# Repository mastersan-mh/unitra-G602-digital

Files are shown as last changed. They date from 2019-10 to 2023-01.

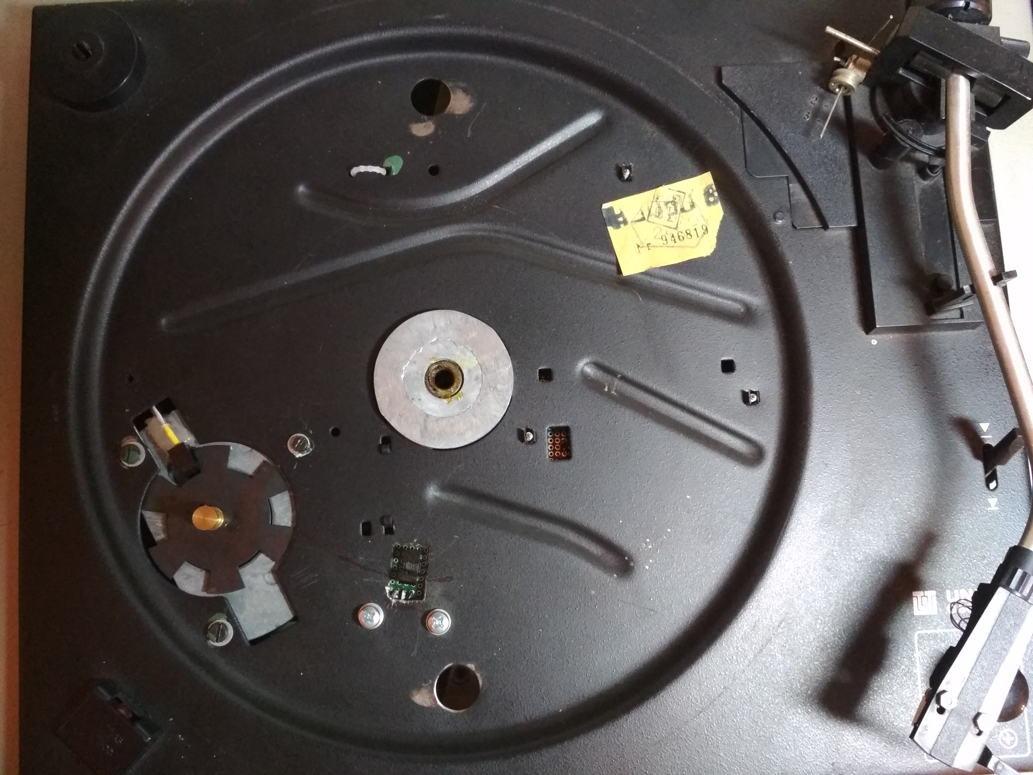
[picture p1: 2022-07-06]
rev1/pictures/IMG_20191018_183628.jpg

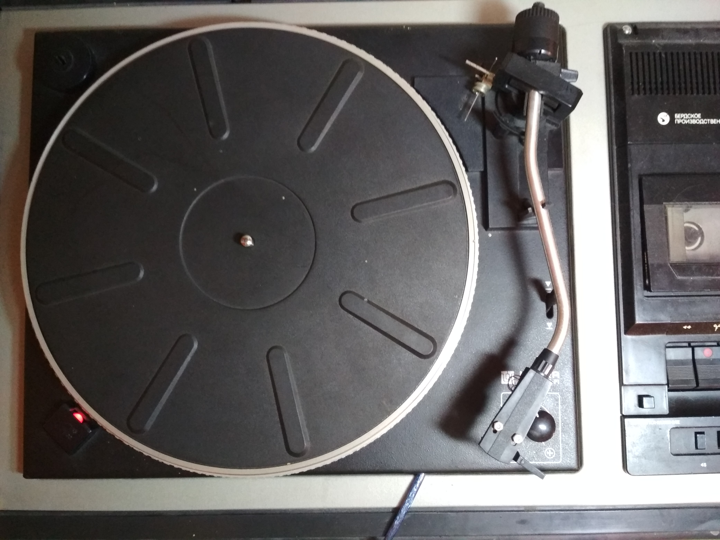
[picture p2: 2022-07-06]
rev1/pictures/IMG_20191018_184000.jpg

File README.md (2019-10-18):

I apologize to non-Russian-speaking users for the lack of information in English.

Данный проект был начат мной как попытка реанимировать старый электрофон Вега 119 с ЭПУ Unitra G602
(А ещё я люблю музыку и программирование).
Поскольку у оригинального устройства аналоговая плата управления пришла в полную негодность,
мной было принято решение о разработке цифрового управления.

В качестве платформы я выбрал Arduino Nano на микроконтроллере ATmega328p.
Это сильно упростило разработку платы и монтаж микросхем, особенно учитывая то, что это штучное устройство,
и весь монтаж я планировал провоизводить на макетную плату, используя только выводные компоненты.

Я процессе модернизации я старался как можно меньше модифицировать оригинальный компоненты,
однако, модификации подверглись:

1. Ведомый шкив. К нему снизу были приклеены 8 флажков.
Поскольку мне неизвестно передаточное число для шкива мотора и шкива диска,
я снимаю показания о скорости непосредственно со шкива диска.
Флажки изначально были подобраны такой высоты, чтобы шкив задевал ими за стол и не вращался.
Для того чтобы флажки стали нужной высоты, я покрыл наждачной бумагой стол ЭПУ, и несколько раз повернул шкив вокруг оси.
Как результат, флажки сточились до необходимой высоты.

2. В столе было прорезано одно отверстие, для того чтобы поместить туда оптический датчик для снятия показаний вращения диска,
и расширено одно из отверстий, чтобы в него вставить оптический датчик вращения двигателя.
Оригинальный датчик я не стал оставлять, поскольку его характеристики мне неизвестны,
а так же был сломан держатель лампы, которая освещала его.

3. Крепление двигателя было модифицировано, чтобы в него можно было вставить датчик вращения.

4. Оригиналная лампа стробоскопа была заменена на светодиод, который к тому же используется для индикации состояний.

5. Немного пришлось отрегулировать флажок автостопа, поскольку новый датчик немного не попал на то место, где находился старый датчик.

На самом деле, датчик вращения двигателя не нужен, я решил его установить в качестве эксперимена.

2019-09-29

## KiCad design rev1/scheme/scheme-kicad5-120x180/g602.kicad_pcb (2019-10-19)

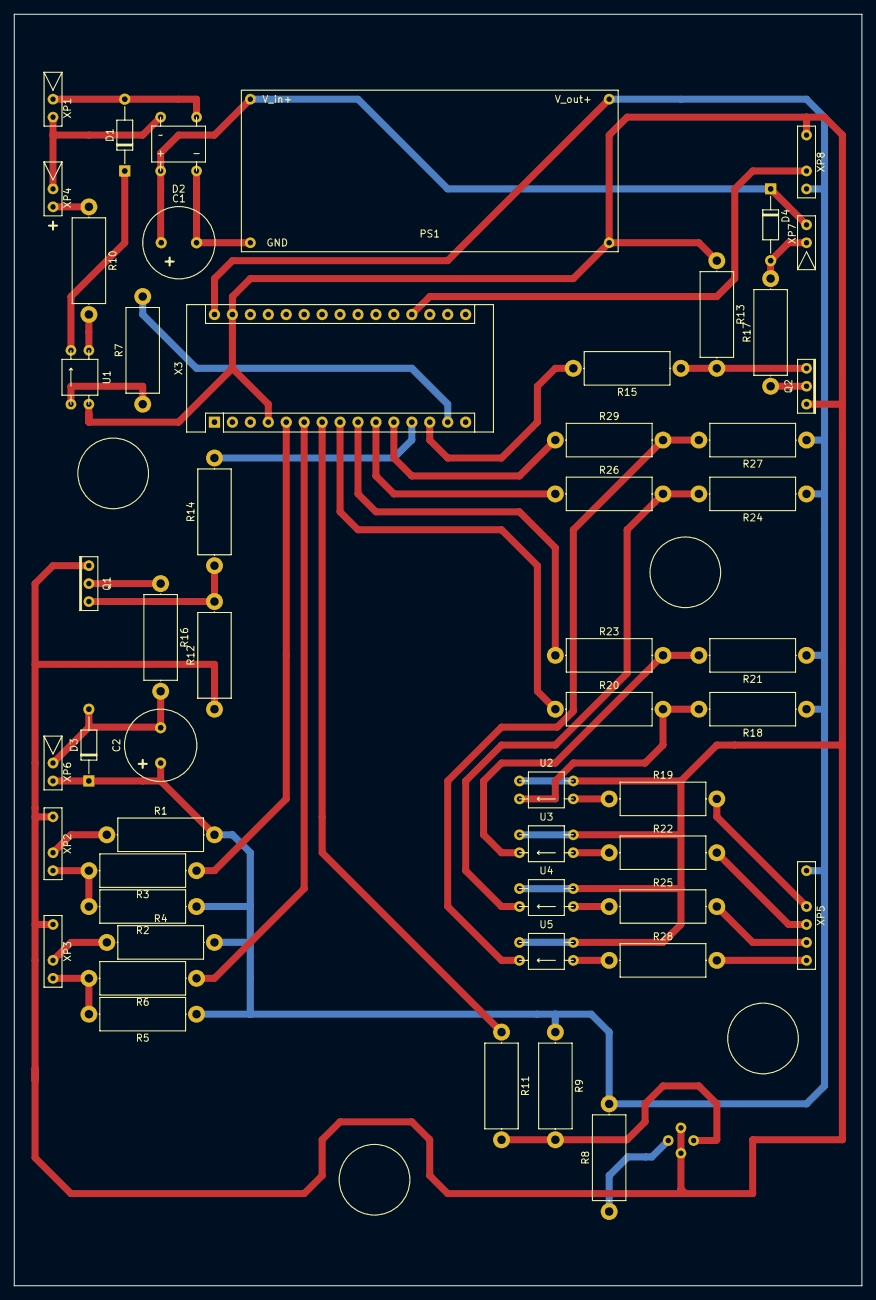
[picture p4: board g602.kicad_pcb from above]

Board: 2 copper layers, 120.0 x 180.0 mm, 53 parts (1 on the bottom side), 45 nets.

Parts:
C1: 2500uF; C_Radial_D10.0mm_H12.5mm_P5.00mm
C2: 2200uF; C_Radial_D10.0mm_H12.5mm_P5.00mm
D1, D3, D4: D; D_DO-35_SOD27_P10.16mm_Horizontal
D2: DF01M
PS1: DC-DC; DC-DC-converter
Q1, Q2: IRL2203NPBF
R1, R4, R7, R8, R19, R22, R25, R28: 510; R_Axial_DIN0414_L11.9mm_D4.5mm_P15.24mm_Horizontal
R2, R5, R9, R18, R21, R24, R27: 10k; R_Axial_DIN0414_L11.9mm_D4.5mm_P15.24mm_Horizontal
R3, R6, R11, R20, R23, R26, R29: 1k; R_Axial_DIN0414_L11.9mm_D4.5mm_P15.24mm_Horizontal
R10: 2k; R_Axial_DIN0414_L11.9mm_D4.5mm_P15.24mm_Horizontal
R12, R13: 50k; R_Axial_DIN0414_L11.9mm_D4.5mm_P15.24mm_Horizontal
R14, R15, R16: 10; R_Axial_DIN0414_L11.9mm_D4.5mm_P15.24mm_Horizontal
R17: 200; R_Axial_DIN0414_L11.9mm_D4.5mm_P15.24mm_Horizontal
U1, U2, U3, U4, U5: PC817
X3: arduino-nano; Arduino_Nano
X4: TCST1103; TCST1103-veritcal
XP1: ~~ 50Hz, 17V; Connector_01x02
XP2: Feedback_drive; Connector_01x03
XP3: Feedback_table; Connector_01x03
XP4: Strobe; Connector_01x02
XP5: Buttons; Connector_01x05
XP6: Motor; Connector_01x02
XP7: Microlift; Connector_01x02
XP8: Manual_speed_adjust; Connector_01x03

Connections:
GNDREF: PS1.3, Q1.3, Q2.3, R12.1, R13.1, U1.2, U2.2, U2.3, U3.2, U3.3, U4.2, U4.3, U5.2, U5.3, X3.4, X3.29, X4.2, X4.4, XP2.1, XP3.1, XP8.1
unnamed: C1.1, D2.1, D4.1, PS1.1, XP7.2
unnamed: C1.2, D2.2, PS1.2
unnamed: C2.1, D3.1, PS1.4, R1.2, R2.1, R4.2, R5.1, R8.2, R9.1, R18.1, R21.1, R24.1, R27.1, X3.30, XP5.1, XP6.2, XP8.3
unnamed: C2.2, D3.2, R16.2, XP6.1
unnamed: D1.1, U1.4
unnamed: D1.2, D2.3, XP1.1
unnamed: D2.4, XP1.2, XP4.1
unnamed: D4.2, R17.2, XP7.1
unnamed: Q1.1, R12.2, R14.1
unnamed: Q1.2, R16.1
unnamed: Q2.1, R13.2, R15.1
unnamed: Q2.2, R17.1
unnamed: R1.1, XP2.2
unnamed: R2.2, R3.2, XP2.3
unnamed: R3.1, X3.5
unnamed: R4.1, XP3.2
unnamed: R5.2, R6.2, XP3.3
unnamed: R6.1, X3.6
unnamed: R7.1, U1.1
unnamed: R7.2, X3.14
unnamed: R8.1, X4.1
unnamed: R10.1, XP4.2
unnamed: R10.2, U1.3
unnamed: R11.1, X3.7
unnamed: R9.2, R11.2, X4.3
unnamed: R14.2, X3.12
unnamed: R15.2, X3.13
unnamed: R18.2, R20.2, U2.4
unnamed: R19.1, U2.1
unnamed: R19.2, XP5.2
unnamed: R20.1, X3.8
unnamed: R21.2, R23.2, U3.4
unnamed: R22.1, U3.1
unnamed: R22.2, XP5.3
unnamed: R23.1, X3.9
unnamed: R24.2, R26.2, U4.4
unnamed: R25.1, U4.1
unnamed: R25.2, XP5.4
unnamed: R26.1, X3.10
unnamed: R27.2, R29.2, U5.4
unnamed: R28.1, U5.1
unnamed: R28.2, XP5.5
unnamed: R29.1, X3.11
unnamed: X3.19, XP8.2

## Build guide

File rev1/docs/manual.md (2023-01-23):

Руководство пользователя устройства электропроигрывающего Unitra-G602(digital)
========

** Содержание **

[TOCM]

[TOC]

# Описание режимов работы

## 1.1 Стоп

  + Описание

    Стол остановлен, лифт поднят.

  + Назначение органов управления

| Орган управления | Действие | Индикация |
| --- | --- | --- |
| `[45]` | Включение базовой скорости 45 об/мин | Нет |
| `[33]` | Включение базовой скорости 33 1/3 об/мин | Нет |
| `[АВТОСТОП]` | Нет | Нет |
| `[ПУСК]` | Переход в режим [1.2] | <1> |
| `[СТОП]` | Нет | Нет |
| `[СТОП]` в течении 5 секунд | Переход в режим [2.1] | <6> |
| `[РЕГУЛЯТОР]` | Нет | Нет |

## 1.2 Воспроизведение с фиксированной скоростью

  + Описание

    Воспроизведение с фиксированной скоростью, выбранной переключателями [45]/[33]. Стол вращается, лифт опущен.

  + Назначение органов управления

| Орган управления | Действие | Индикация |
| --- | --- | --- |
| `[45]` | Смотри режим [1.1] | Нет |
| `[33]` | Смотри режим [1.1] | Нет |
| `[АВТОСТОП]` | Включение режима автоматической остановки стола и поднятия лифта при достижении конца записи | Нет |
| `[ПУСК]` | Переход в режим [1.3] | <5> |
| `[СТОП]` | Переход в режим [1.1] | <2> |
| `[РЕГУЛЯТОР]` | Нет | Нет |

## 1.3 Воспроизведение с регулируемой скоростью

  + Описание

    Воспроизведение со скоростью, выбранной переключателями [45]/[33] с возможность ручной подстройки регулятором [РЕГУЛЯТОР]:
    для базовой скорости 45 - в диапазоне от 39 до 51, для базовой скорости 33 - в диапазоне от 27 до 39 об/мин.
    Стол вращается, лифт опущен.

  + Назначение органов управления

| Орган управления | Действие | Индикация |
| --- | --- | --- |
| `[45]` | Смотри режим [1.1] | Нет |
| `[33]` | Смотри режим [1.1] | Нет |
| `[АВТОСТОП]` | Смотри режим [1.2] | Нет |
| `[ПУСК]` | Переход в режим [1.2] | <5> |
| `[СТОП]` | Переход в режим [1.1] | <2> |
| `[РЕГУЛЯТОР]` | Ручная подстройка скорости воспроизведения | Нет |

## 2.1. Сервисный режим #1

  + Описание

    Режим настройки иглы: Стол остановлен, лифт опущен.

  + Назначение органов управления

| Орган управления | Действие | Индикация |
| --- | --- | --- |
| `[45]` | Смотри режим [1.1] | Нет |
| `[33]` | Смотри режим [1.1] | Нет |
| `[АВТОСТОП]` | Смотри режим [1.2] | Нет |
| `[ПУСК]` | Запуск режима | Нет |
| `[СТОП]` | Остановка режима / Переход в режим [2.2] | <2> / <4> |
| `[РЕГУЛЯТОР]` | Нет | Нет |

## 2.2. Сервисный режим #2

  + Описание

    Режим настройки скатывания иглы: Стол вращается, лифт опущен

  + Назначение органов управления

| Орган управления | Действие | Индикация |
| --- | --- | --- |
| `[45]` | Смотри режим [1.1] | Нет |
| `[33]` | Смотри режим [1.1] | Нет |
| `[АВТОСТОП]` | Смотри режим [1.2] | Нет |
| `[ПУСК]` | Запуск режима | Нет |
| `[СТОП]` | Остановка режима / Переход в режим [2.3] | <2> / <5> |
| `[РЕГУЛЯТОР]` | Нет | Нет |

## 3.3. Сервисный режим #3

  + Описание

    Настройки регулятора скорости внешними командами, принятыми из последовательного порта

  + Назначение органов управления

| Орган управления | Действие | Индикация |
| --- | --- | --- |
| `[45]` | Смотри режим [1.1] | Нет |
| `[33]` | Смотри режим [1.1] | Нет |
| `[АВТОСТОП]` | Смотри режим [1.2] | Нет |
| `[ПУСК]` | Запуск режима | Нет |
| `[СТОП]` | Остановка режима / Переход в режим [1.1] | <2> / <6> |
| `[РЕГУЛЯТОР]` | Нет | Нет |

# Индикация

| № | Тип мигания | Тип мигания | Значение |
| - | --- | --- | --- |
| 1 | `*-**--***---****----*****` | Ускоряющееся мигание | Запуск воспроизведения |
| 2 | `*****-----****----***---**--*` | Замедляющееся мигание | Остановка воспроизведения |
| 3 | `**` | 1 мигание | Включено автоматическое упавление скоростью / Переход в сервисный режим #1 |
| 4 | `**--**` | 2 мигание | Переход в сервисный режим #2 |
| 5 | `**--**--**` | 3 мигания | Включено ручное упавление скоростью / Переход в сервисный режим #3 |
| 6 | `*-*-*-*-*-*` | Частое мигание 6 раз | Переход в меню переключения сервисных режимов / Выход из меню сервисных режимов |
| 7 | `***---...` | медленное непрерывное мигание | Торможение стола выбегом |
| 8 | `*-...` | частое непрерывное мигание | Разгон стола |

# Протокол коммуникации посредством последовательного порта

## Назначение

Коммуникация посредством последовательного порта нужна для отладки изделия и для настройки коэффициентов регулятора скорости стола.

## Формат команды

Команды представляют собой набор ASCII-символов в 8-битной кодировке. Все числа представляются в 16-ричном формате,
цифры представлены множеством символов 0, 1, 2, 3, 4, 5, 6, 7, 8, 9, A, B, C, D, E, F.

* Формат кадра нижнего уровня:

`<start><frame><CRC><stop>`

`<start>`   - символ ':'.

`<stop>`    - Любой из символов LF (0x0A, '\n'), CR (0x0D, '\r') и их сочетания, 1-2 байта. В кадре ответа всегда LF.
              Любые внекадровые символы CR/LF игнорируются.

`<CRC>`     - Контрольная сумма <frame>, 16 бит, CRC-16-IBM, полином 0xA001.

* Кадр запроса:

`<frame> = <ruid><funcid><argc><argv>`

`<ruid>`     - [16 бит] Произвольное число, испрользуется для идентификации запроса и ответа. Ответ содержит то-же число, что и запрос.

`<funcid>`   - [8 бит] Код функции.

`<argc>`     - [8 бит] Количество аргументов [0; 8]

`<argv>`     - [16 * <argc> бит] Вектор аргументов.

* Кадр ответа:

`<frame> = <type>{ <ruid><error><resc><resv> | <eventid><resc><resv> }`

`<type>`     - [8 бит] тип ответа: 0x00 - ответ на вызов процедуры; 0x01 - событие

`<error>`    - [8 бит] Код ошибки.

`<eventid>`  - [8 бит] Код события.

`<resc>`     - [8 бит] Количество чисел в ответе.

`<resv>`     - [16 * <resc> бит] Вектор ответов.

Приечание: старший байт стоит первым (Network byte order)

## Функции

1. Прочитать значение количества имульсов на один оборот стола.

    * Запрос:

    `<funcid> = 0x00`

    `<argc> = 0`

    * Ответ:

    `<resc> = 1`

    `<argv[0]>` - Количество импульсов на один оборот стола.

    + Доступность: Все режимы

    + Пример:

      + Запрос: ":abcd0000ffb1\n"

      + Ответ: ":00abcd00010004087f\n"

2. Прочитать номер режима.

    * Запрос:

    `<funcid> = 0x01`

    `<argc> = 0`

    * Ответ:

    `<resc> = 1`

    `<resv[0]>` - номер режима (расшифровку смотри в ```Приложение:Коды значений```).

   * Доступность: Все режимы

   * Пример:

      + Запрос: ":abcd01006fb0\n"

      + Ответ: ":00abcd000110000b73\n"
             ":00abcd00011001cbb2\n"

3. Прочитать коэффициенты ПИД-регулятора: Kp, Ki, Kd

    * Запрос:

    `<funcid> = 0x02`

    `<argc> = 0`

    * Ответ:

    `<resc> = 6`

    `<resv[0]>`, `<resv[1]>` - `<Kp>`, пропорциональный коэффициент в формате signed-fixed-point-16.16.

    `<resv[2]>`, `<resv[3]>` - `<Ki>`, интегральный коэффициент в формате signed-fixed-point-16.16.

    `<resv[4]>`, `<resv[5]>` - `<Kd>`, дифференциальный коэффициент в формате signed-fixed-point-16.16

    * Доступность: Все режимы

4. Задать коэффициенты ПИД-регулятора: Kp, Ki, Kd

    * Запрос:

    `<funcid> = 0x03`

    `<argc> = 6`

    `<argv[0]>`, `<argv[1]>` - `<Kp>`, пропорциональный коэффициент в формате signed-fixed-point-16.16.

    `<argv[2]>`, `<argv[3]>` - `<Ki>`, интегральный коэффициент в формате signed-fixed-point-16.16.

    `<argv[4]>`, `<argv[5]>` - `<Kd>`, дифференциальный коэффициент в формате signed-fixed-point-16.16

    * Ответ:

    `<resc> = 0`

    + Доступность: Режим 2.3

5. Прочитать уставку скорости вращения стола

    * Запрос:

    `<funcid> = 0x04`

    `<argc> = 0`

    * Ответ:

    `<resc> = 2`

    `<resv[0]>`, `<resv[1]>` - Скорость вращения, число в диапазоне  `[0; 51 * <imp>]` импульсов/мин в формате signed-fixed-point-16.16.

    + Доступность: Все режимы

6. Задать уставку скорости вращения стола

    * Запрос:

    `<funcid> = 0x05`

    `<argc> = 2`

    `<argv[0]>`, `<argv[1]>` - Скорость вращения, число в диапазоне  `[ 0; 51 * <imp> ]` импульсов/мин в формате signed-fixed-point-16.16.

    * Ответ:

    `<resc> = 0`

    + Доступность: Режим 2.3

7. Прочитать действительную скорость вращения стола

    * Запрос:

    `<funcid> = 0x06`

    `<argc> = 0`

    * Ответ:

    `<resc> = 2`

    `<resv[0]>`, `<resv[1]>` - Скорость вращения, число в диапазоне  `[ 0; 51 * <imp> ]` импульсов/мин в формате signed-fixed-point-16.16.

    + Доступность: Все режимы

8. Запустить непрерывную передачу SP/PV

    * Запрос:

    `<funcid> = 0x07`

    `<argc> = 0`

    * Ответ:

    `<resc> = 0`

    + Доступность: Все режимы

9. Остановить непрерывную передачу SP/PV

    * Запрос:

    `<funcid> = 0x08`

    `<argc> = 0`

    * Ответ:

    `<resc> = 0`

    + Доступность: Все режимы

10. Сохранить конфигурацию

    * Запрос:

    `<funcid> = 0x09`

    `<argc> = 0`

    * Ответ:

    `<resc> = 0`

    + Доступность: Режим 2.3

## События

1. Событие переключения режима

     Событие инициируется при переключении режима работы.

    `<eventid>` = 0x00

    `<resc> = 1`

    `<resv[0]>` - Режим, смотри `<funcid> = 0x00`.

2. Событие SP/PV

     Событие всегда происходит через равные промежутки времени.

    `<eventid>` = 0x01

    `<resc> = 8`

    `<resv[0]>`, `<resv[1]>` - Время от запуска микроконтроллера, старшая и младшая часть, мс.

    `<resv[2]>`, `<resv[3]>` - Setpoint (Уставка), cкорость вращения, число в диапазоне  `[0; 51 * <imp>]` импульсов/мин в формате signed-fixed-point-16.16.

    `<resv[4]>`, `<resv[5]>` - Process Variable (Переменная процесса), cкорость вращения, число в диапазоне `[0; 51 * <imp>]` импульсов/мин в формате signed-fixed-point-16.16.

    `<resv[6]>`, `<resv[7]>` - Переменная управления в формате signed-fixed-point-16.16

    * Примечание:
        Переменная управления показывает значение, полученое с регулятора, однако, на привод отправляется только целая часть числа в диапазоне [0; 255]

# Приложение

## Коды ошибок

| Код(hex) | Описание |
| --- | --- |
| 0x00 | Нет ошибок |
| 0x01 | Команда недоступна в этом режиме |
| 0x02 | Неправильное количество аргументов |
| 0x03 | Значение агрумента вне диапазона |

## Коды значений

| Значение номера режима | Режим |
| --- | --- |
| 0x1000 | 1.1 |
| 0x1001 | 1.2 |
| 0x1002 | 1.3 |
| 0x2100 | 2.1: stopped |
| 0x2101 | 2.1: started |
| 0x2200 | 2.2: stopped |
| 0x2201 | 2.2: started |
| 0x2300 | 2.3: stopped |
| 0x2301 | 2.3: started |

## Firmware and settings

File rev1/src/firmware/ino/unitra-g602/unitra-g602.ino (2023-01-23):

#include "config.hpp"

#include "defs.hpp"

#include "AverageTinyMemory.hpp"

#include "G602.hpp"

#include "utils.hpp"

#include <nostd-main.h>
#include <nostd.h>

#include <util/atomic.h>
#include <EEPROM.h>

DEBUG_INIT_GLOBAL();

/*

/home/mastersan/progs/arduino-nightly/hardware/arduino/avr/cores/arduino
/home/mastersan/progs/arduino-nightly/hardware/arduino/avr/variants/standard
/home/mastersan/progs/arduino-nightly/hardware/tools/avr/avr/include




/home/mastersan/progs/arduino-nightly/hardware/tools/avr/bin/avr-g++
-c
-g
-Os
-w
-std=gnu++11
-fpermissive
-fno-exceptions
-ffunction-sections
-fdata-sections
-fno-threadsafe-statics
-Wno-error=narrowing
-flto
-w
-x c++
-E
-CC
-mmcu=atmega328p
-DF_CPU=16000000L
-DARDUINO=10807
-DARDUINO_AVR_NANO
-DARDUINO_ARCH_AVR
-I/home/mastersan/progs/arduino-nightly/hardware/arduino/avr/cores/arduino
-I/home/mastersan/progs/arduino-nightly/hardware/arduino/avr/variants/eightanaloginputs
/tmp/arduino_build_724020/sketch/unitra-g602.ino.cpp
-o /dev/null

*/

#define BOOL_TO_STR(xval) (xval ? "true" : "false")

//#define rotate_pulse_counter_t unsigned int
using rotate_pulse_counter_t = unsigned int;

static unsigned long g_time;
static unsigned long g_time_prev = 0;
static unsigned long c_cycletime = 0;

template<typename T>
T utils_map(T x, T in_min, T in_max, T out_min, T out_max)
{
    return (x - in_min) * (out_max - out_min) / (in_max - in_min) + out_min;
}

void dump_u8(
        const uint8_t * data ARG_UNUSED,
        unsigned size
)
{
    unsigned i;
    DEBUG_PRINT("  size8 = ");
    DEBUG_PRINTLN(size);
    for(i = 0; i < size; ++i)
    {
        DEBUG_PRINT("  data8[");
        DEBUG_PRINT(i);
        DEBUG_PRINT("]=");
        DEBUG_PRINTLN(data[i]);
    }
}

void dump_u16(
        const uint16_t * data ARG_UNUSED,
        unsigned size
)
{
    unsigned i;
    DEBUG_PRINT("  size16 = ");
    DEBUG_PRINTLN(size);
    for(i = 0; i < size; ++i)
    {
        DEBUG_PRINT("  data16[");
        DEBUG_PRINT(i);
        DEBUG_PRINT("]=");
        DEBUG_PRINTLN(data[i]);
    }
}

static void terminate_handler(const char * file, unsigned int line, int error)
{
#define BLINK_PERIOD_MS 250
    static long time_prev = 0;
    static long time;
    static bool on = true;

    unsigned long x = (unsigned long)file + line + error; /* to suppress warnings */

    while(1)
    {
        time = millis();
        if(time - time_prev >= BLINK_PERIOD_MS)
        {
            time_prev = time;
            if(x == 0)
            {
                digitalWrite(PIN_DO_STROBE_ERROR, on ? HIGH : LOW);
            }
            digitalWrite(PIN_DO_STROBE_ERROR, on ? HIGH : LOW);
            on = !on;
        }
    }
}

struct pulse
{
    unsigned long change_time; /**< Time of change */
    rotate_pulse_counter_t pulses; /**< Amount of clean pulses */
    rotate_pulse_counter_t bounces; /**< Amount of bounces (dirty pulses) */
};

static volatile struct pulse P_motor_rotate;
static volatile struct pulse P_table_rotate;

static void P_pulse_get(
        volatile struct pulse * pulse_in,
        bool reset,
        struct pulse * pulse_out
)
{
    pulse_out->change_time = pulse_in->change_time;
    pulse_out->pulses = pulse_in->pulses;
    pulse_out->bounces = pulse_in->bounces;
    if(reset)
    {
        pulse_in->pulses = 0;
        pulse_in->bounces = 0;
    }
}

void P_pulses_all_get(
        struct pulse * pulses_motor,
        struct pulse * pulses_table,
        bool reset
)
{
    ATOMIC_BLOCK(ATOMIC_FORCEON)
    {
        P_pulse_get(&P_motor_rotate, reset, pulses_motor);
        P_pulse_get(&P_table_rotate, reset, pulses_table);
    }
}

void P_config_store(const uint8_t * conf, size_t size)
{
    unsigned i;
    for(i = 0; i < size; ++i)
    {
        EEPROM.write(i, conf[i]);
    }
}

void P_config_load(uint8_t * conf, size_t size, bool * empty)
{
    bool tempty = true;
    unsigned i;
    for(i = 0; i < size; ++i)
    {
        for(i = 0; i < size; ++i)
        {
            conf[i] = EEPROM.read(i);
            if(conf[i] != 255)
            {
                tempty = false;
            }
        }
    }
    (*empty) = tempty;
}

static void P_event_strober(bool on)
{
    digitalWrite(PIN_DO_STROBE_ERROR, (on ? HIGH : LOW));
}

static void P_event_lift_up()
{
    digitalWrite(PIN_DO_LIFT, LOW);
    digitalWrite(PIN_DO_AUDIO_DENY, LOW);
}

static void P_event_lift_down()
{
    digitalWrite(PIN_DO_LIFT, HIGH);
    digitalWrite(PIN_DO_AUDIO_DENY, HIGH);
}

void P_motor_update(bool state, int output)
{
    if(state)
    {
        analogWrite(PIN_DO_ENGINE, output);
    }
    else
    {
        analogWrite(PIN_DO_ENGINE, 0);
    }
}

static void P_pulses_get(unsigned * motor_dpulses, unsigned * table_dpulses)
{
    struct pulse m_pulse;
    struct pulse t_pulse;
    P_pulses_all_get(&m_pulse, &t_pulse, true); /* reset */
    (*motor_dpulses) = m_pulse.pulses;
    (*table_dpulses) = t_pulse.pulses;

#if 0
    DEBUG_PRINT(g_time);

    DEBUG_PRINT("\tpulses ");
    DEBUG_PRINT(t_pulse.pulses);
    DEBUG_PRINT("\tbounces ");
    DEBUG_PRINT(t_pulse.bounces);

    DEBUG_PRINTLN();
#endif

}

static G602 g602(
    P_config_store,
    P_config_load,
    P_event_strober,
    P_event_lift_up,
    P_event_lift_down,
    P_motor_update,
    P_pulses_get
);

void P_pulses_init(volatile struct pulse * pulse)
{
    pulse->change_time = g_time;
    pulse->pulses = 0;
    pulse->bounces = 0;
}

static void P_pulse_update(volatile struct pulse * pulse, unsigned long bounce_time)
{
    if(g_time - pulse->change_time >= bounce_time)
    {
        ++(pulse->pulses);
    }
    else
    {
        ++(pulse->bounces);
    }
    pulse->change_time = g_time;
}

void drive_rotate_pulse_update(void)
{
    P_pulse_update(&P_motor_rotate, DI_MOTOR_DEBOUNCE_TIME);
}

void table_rotate_pulse_update(void)
{
    P_pulse_update(&P_table_rotate, DI_TABLE_DEBOUNCE_TIME);
}

static AverageTinyMemory potentiometer_avg(DI_POTENTIOMETER_FACTOR);

void setup()
{
    Serial.begin(9600);

    DEBUG_PRINT_INIT();

    g_time = millis();

    nostd::set_fatal(terminate_handler);
    /* INFO: разомкнуто = HIGH */

    /* gauges */
    pinMode(PIN_DI_GAUGE_DRIVE_ROTATEPULSE, INPUT_PULLUP);
    attachInterrupt(PIN_DI_2_INTERRUPT, drive_rotate_pulse_update, FALLING);
    pinMode(PIN_DI_GAUGE_TABLE_ROTATEPULSE, INPUT_PULLUP);
    attachInterrupt(PIN_DI_3_INTERRUPT, table_rotate_pulse_update, FALLING);

    pinMode(PIN_DI_GAUGE_STOP         , INPUT_PULLUP);
    /* buttons */
    pinMode(PIN_DI_BTN_45_33   , INPUT_PULLUP);
    pinMode(PIN_DI_BTN_AUTOSTOP, INPUT_PULLUP);
    pinMode(PIN_DI_BTN_START   , INPUT_PULLUP);
    pinMode(PIN_DI_BTN_STOP    , INPUT_PULLUP);

    pinMode(PIN_DO_ENGINE      , OUTPUT);
    pinMode(PIN_DO_LIFT        , OUTPUT);
    pinMode(PIN_DO_STROBE_ERROR, OUTPUT);
    pinMode(PIN_DO_AUDIO_DENY  , OUTPUT);

    analogWrite(PIN_DO_ENGINE, 0);
    digitalWrite(PIN_DO_STROBE_ERROR, HIGH);
    digitalWrite(PIN_DO_AUDIO_DENY  , LOW);

    analogReference(DEFAULT);

    P_pulses_init(&P_motor_rotate);
    P_pulses_init(&P_table_rotate);

}

void loop()
{
    g_time_prev = g_time;
    g_time = millis();
    c_cycletime = g_time - g_time_prev;

    g602.timeSet(g_time);

    /* sensors */
    g602.notifyGaugeStopSet(digitalRead(PIN_DI_GAUGE_STOP) == LOW);
    /* buttons */
    g602.notifyButtonSpeedModeSet(digitalRead(PIN_DI_BTN_45_33) == LOW);
    g602.notifyButtonAutostopSet(digitalRead(PIN_DI_BTN_AUTOSTOP) == LOW);
    g602.notifyButtonStartSet(digitalRead(PIN_DI_BTN_START) == LOW);
    g602.notifyButtonStopSet(digitalRead(PIN_DI_BTN_STOP) == LOW);

    /* potentiometer */
    int val = analogRead(PIN_AI_POTENTIOMETER); /* 10 bits */
    potentiometer_avg.appendValue(val);
    int avg = potentiometer_avg.averageGet();

#define POTENTIOMETER_TO_MANUAL_SPEED(xval) \
        utils_map( \
                Speed(xval, Speed::tag_int), \
                Speed(G602_POTENTIOMETER_MIN, Speed::tag_int), \
                Speed(G602_POTENTIOMETER_MAX, Speed::tag_int), \
                Speed(G602_SPEED_RANGE_MIN, Speed::tag_double), \
                Speed(G602_SPEED_RANGE_MAX, Speed::tag_double) \
        )
    const Speed speed_manual = POTENTIOMETER_TO_MANUAL_SPEED(avg);

    g602.manualSpeedSet(speed_manual);

    g602.loop();
}

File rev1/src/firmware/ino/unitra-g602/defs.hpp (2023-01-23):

#ifndef DEFS_H_
#define DEFS_H_

#include "Speed.hpp"

/* button debounce time, ms */
#define DI_DEBOUNCE_TIME (100UL)

#define DI_MOTOR_DEBOUNCE_TIME (2U)
#define DI_TABLE_DEBOUNCE_TIME (50U)

#define DI_POTENTIOMETER_FACTOR 10

/* irq 0 (digital pin 2) */
#define PIN_DI_2_INTERRUPT (0U)
/* irq 1 (digital pin 3) */
#define PIN_DI_3_INTERRUPT (1U)

#define PIN_DI_GAUGE_DRIVE_ROTATEPULSE (2U)
#define PIN_DI_GAUGE_TABLE_ROTATEPULSE (3U)
#define PIN_DI_GAUGE_STOP        (4U)
#define PIN_DI_BTN_45_33    (5U)
#define PIN_DI_BTN_AUTOSTOP (6U)
#define PIN_DI_BTN_START    (7U)
#define PIN_DI_BTN_STOP     (8U)
#define PIN_DO_ENGINE       (9U)
#define PIN_DO_LIFT         (10U)
#define PIN_DO_STROBE_ERROR (11U)
#define PIN_DO_AUDIO_DENY   (12U)

#define PIN_AI_POTENTIOMETER (PIN_A0)

#define G602_POTENTIOMETER_HALF 512 /* full scale of potentiometer = 1024 -> 1024/2 */
#define G602_POTENTIOMETER_MIN 0 /* 0 */
#define G602_POTENTIOMETER_MAX (G602_POTENTIOMETER_HALF * 2 - 1) /* full scale of potentiometer = 1024 -> 1024/2 */

#define G602_EVENT_MODE_CHANGED 0x00
#define G602_EVENT_SPPV 0x01

#define G602_SHEDULER_TASKS__NUM 3

/* Amount of impulses per revolution */
#define G602_ENGINE_PULSES_PER_REV 6
#define G602_TABLE_PULSES_PER_REV 16

/** @brief Speeds of table, rpm */
#define G602_TABLE_SPEED_LOW_RPM  (33.0 + 1.0/3.0)
#define G602_TABLE_SPEED_HIGH_RPM (45.0)

#define G602_SPEED_HALF          ((G602_SPEED_BASELINE_HIGH - G602_SPEED_BASELINE_LOW) / 2)
#define G602_SPEED_RANGE_MIN     (-G602_SPEED_HALF)
#define G602_SPEED_RANGE_MAX     (G602_SPEED_HALF)
#define G602_SPEED_MIN           (G602_SPEED_BASELINE_LOW - G602_SPEED_HALF)
#define G602_SPEED_BASELINE_LOW  (G602_TABLE_SPEED_LOW_RPM)
#define G602_SPEED_BASELINE_HIGH (G602_TABLE_SPEED_HIGH_RPM)
#define G602_SPEED_MAX           (G602_SPEED_BASELINE_HIGH + G602_SPEED_HALF)

/* Time(ms) for which <xppr> pulses are counted at the <xspeed> speed. */
#define G602_MINIMAL_TIME(xppr, xspeed) ((60UL * 1000UL * (unsigned long)(xppr)) / (unsigned long)(xspeed))

#define G602_MINIMAL_TIME_OF_MINIMAL_SPEED      G602_MINIMAL_TIME(G602_TABLE_PULSES_PER_REV, G602_SPEED_MIN)

#define G602_PID_DEFAULT_KP 0.93750000
#define G602_PID_DEFAULT_KI 0.31250000
#define G602_PID_DEFAULT_KD 0.15625000

/* Use the speed error indication filter */
// #define G602_USE_FILTER

#endif

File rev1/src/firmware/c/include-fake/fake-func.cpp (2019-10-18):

/**
 * @file fake.cpp
 */

#include <Arduino.h>
#include "../config.hpp"

void setup();
void loop();


int main()
{
    setup();
    while(1)
    {
        loop();
    }
    return EXIT_SUCCESS;
}

void attachInterrupt(uint8_t, void (*)(void), UNUSED int mode)
{

}

void digitalWrite(UNUSED uint8_t pin, uint8_t)
{

}

int digitalRead(UNUSED uint8_t pin)
{
    return 0;
}

void analogReference(UNUSED uint8_t mode)
{

}

int analogRead(UNUSED uint8_t pin)
{
    return 0;
}

void analogWrite(UNUSED uint8_t pin, UNUSED int value)
{

}

void pinMode(UNUSED uint8_t pin, uint8_t)
{

}

long map(UNUSED long value, UNUSED long fromLow, UNUSED long fromHigh, UNUSED long toLow, UNUSED long toHigh)
{
    return 0;
}

unsigned long millis(void)
{
    return 0;
}

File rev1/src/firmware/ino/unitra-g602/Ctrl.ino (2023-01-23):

#include "Ctrl.hpp"

#define ARRAY_INDEX(x) static_cast<unsigned int>(x)

Speed Ctrl::P_speed_baseline_get() const
{
    return m_speed_baselines[ARRAY_INDEX(m_speed_baseline_mode)];
}

void Ctrl::P_event(Event event, const EventData& data, void * args) const
{
    if(m_eventFunc)
    {
        m_eventFunc(event, data, args);
    }
}

void Ctrl::P_event_warnings_set(unsigned warn, void * args)
{
    unsigned old = m_state_warnings;
    m_state_warnings |= warn;
    if(m_state_warnings != old)
    {
        m_eventData.WARNINGS_UPDATE.warnings = m_state_warnings;
        P_event(Event::WARNINGS_UPDATE, m_eventData, args);
    }
}

void Ctrl::P_event_warnings_clean(unsigned warn, void * args)
{
    unsigned old = m_state_warnings;
    m_state_warnings &= ~warn;
    if(m_state_warnings != old)
    {
        m_eventData.WARNINGS_UPDATE.warnings = m_state_warnings;
        P_event(Event::WARNINGS_UPDATE, m_eventData, args);
    }
}

void Ctrl::P_event_motor_on(void * args)
{
    m_motor_state_cached = true;
    P_event(Event::MOTOR_ON, m_eventData, args);
}

void Ctrl::P_event_motor_off(void * args)
{
    m_motor_state_cached = false;
    P_event(Event::MOTOR_OFF, m_eventData, args);
}

void Ctrl::P_event_motor_setpoint_update(Speed setpoint, void * args)
{
    m_motor_speed_SP_cached = setpoint;
    m_eventData.MOTOR_SETPOINT_UPDATE.setpoint = setpoint;
    P_event(Event::MOTOR_SETPOINT_UPDATE, m_eventData, args);
}

void Ctrl::P_event_lift_up(void * args)
{
    P_event(Event::LIFT_UP, m_eventData, args);
}

void Ctrl::P_event_lift_down(void * args)
{
    P_event(Event::LIFT_DOWN, m_eventData, args);
}

void Ctrl::P_event_runmode_changed(RunMode runMode, void * args)
{
    m_eventData.RUNMODE_CHANGED.runMode = runMode;
    P_event(Event::RUNMODE_CHANGED, m_eventData, args);
}

Ctrl::RunMode Ctrl::P_runModeGet(State state)
{
    static const RunMode table[] =
    {
        [ARRAY_INDEX(State::INIT                 )] = RunMode::NORMAL_STOPPED,
        [ARRAY_INDEX(State::NORMAL_STOPPED       )] = RunMode::NORMAL_STOPPED,
        [ARRAY_INDEX(State::NORMAL_STARTED_AUTO  )] = RunMode::NORMAL_STARTED_AUTO,
        [ARRAY_INDEX(State::NORMAL_STARTED_MANUAL)] = RunMode::NORMAL_STARTED_MANUAL,
        [ARRAY_INDEX(State::SERVICE_MODE1_STOPPED)] = RunMode::SERVICE_MODE1_STOPPED,
        [ARRAY_INDEX(State::SERVICE_MODE1_STARTED)] = RunMode::SERVICE_MODE1_STARTED,
        [ARRAY_INDEX(State::SERVICE_MODE2_STOPPED)] = RunMode::SERVICE_MODE2_STOPPED,
        [ARRAY_INDEX(State::SERVICE_MODE2_STARTED)] = RunMode::SERVICE_MODE2_STARTED,
        [ARRAY_INDEX(State::SERVICE_MODE3_STOPPED)] = RunMode::SERVICE_MODE3_STOPPED,
        [ARRAY_INDEX(State::SERVICE_MODE3_STARTED)] = RunMode::SERVICE_MODE3_STARTED,
    };
    return table[ARRAY_INDEX(state)];
}

Ctrl::Error Ctrl::P_fsm(Command cmd, const CommandData & data, void * args)
{
    State next_state = m_state;
    switch(m_state)
    {
        case State::INIT:
        {
             P_event_motor_off(args);
             P_event_lift_up(args);
             const Speed speed = P_speed_baseline_get();
             P_event_motor_setpoint_update(speed, args);
             next_state = State::NORMAL_STOPPED;
             break;
        }

        case State::NORMAL_STOPPED:
        {
            switch(cmd)
            {
                case Command::INIT:
                {
                    break;
                }
                case Command::ENTER_MODE_NORMAL:
                {
                    break;
                }
                case Command::ENTER_SERVICE_MODE1:
                {
                    next_state = State::SERVICE_MODE1_STOPPED;
                    break;
                }
                case Command::ENTER_SERVICE_MODE2:
                {
                    next_state = State::SERVICE_MODE2_STOPPED;
                    break;
                }
                case Command::ENTER_SERVICE_MODE3:
                {
                    next_state = State::SERVICE_MODE3_STOPPED;
                    break;
                }
                case Command::START:
                {
                    if(!(m_state_allowed_autostop && m_state_autostop_triggered))
                    {
                        const Speed speed = P_speed_baseline_get();
                        P_event_motor_setpoint_update(speed, args);
                        P_event_motor_on(args);
                        P_event_lift_down(args);
                        next_state = State::NORMAL_STARTED_AUTO;
                    }
                    break;
                }
                case Command::STOP:
                {
                    break;
                }
                case Command::SPEED_BASELINE_LOW:
                {
                    m_speed_baseline_mode = BaselineSpeedMode::MODE_LOW;
                    break;
                }
                case Command::SPEED_BASELINE_HIGH:
                {
                    m_speed_baseline_mode = BaselineSpeedMode::MODE_HIGH;
                    break;
                }
                case Command::SPEED_MANUAL_UPDATE:
                {
                    m_speed_SP_manual_delta = data.SPEED_MANUAL_UPDATE.speed;
                    break;
                }
                case Command::SPEED_FREE_UPDATE:
                {
                    m_speed_SP_free = data.SPEED_FREE_UPDATE.speed;
                    break;
                }
                case Command::AUTOSTOP_ALLOW:
                {
                    m_state_allowed_autostop = true;
                    break;
                }
                case Command::AUTOSTOP_DENY:
                {
                    m_state_allowed_autostop = false;
                    break;
                }
                case Command::GAUGE_STOP_ON:
                {
                    m_state_autostop_triggered = true;
                    break;
                }
                case Command::GAUGE_STOP_OFF:
                {
                    m_state_autostop_triggered = false;
                    break;
                }
            }
            break;
        }
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

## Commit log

2019-09-27 (refs scheme) Scheme added.
    [g602.kicad_pcb, g602.sch]
2019-09-27 (refs scheme) Resisor updated.
    [g602.kicad_pcb, g602.sch]
2019-09-28 (refs src) button fixed.
    [GDInput.ino, unitra-g602.ino]
2019-09-28 (refs src) src: fixed speed measuring.
    [unitra-g602.ino]
2019-10-01 (refs src) warnings fixed, blinks updated.
    [G602.ino, GBlinker.ino, unitra-g602.ino]
2019-10-02 (refs src) tools draft added (PID).
2019-10-09 (refs src) Draft of Device class added.
2019-10-10 (refs src) Device class draft in progress.
2019-10-12 (refs src) fix firmware, fix tool.
    [G602.ino, GCommBase.ino, GRPCServer.ino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]
2019-10-12 (refs src) pid koef fixed.
    [G602.ino, GRPCServer.ino]
2019-10-15 (refs src) firmware and tool draft fix.
    [Ctrl.hpp, Ctrl.ino, G602.ino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]
2019-10-15 (refs src) pid fixed.
    [G602.ino, unitra-g602.ino]
2019-10-15 (refs src) potentiometer fixed.
    [defs.hpp, unitra-g602.ino]
2019-10-15 (refs src) moto state updating fixed.
    [G602.ino, unitra-g602.ino]
2019-10-16 (refs src) files structure changed.
    [g602.kicad_pcb, g602.sch]
2019-10-17 (refs src) event send on autostop fixed.
    [Ctrl.hpp, Ctrl.ino, G602.ino]
2019-10-17 (refs src) double scheduling fixed.
    [G602.ino]
2019-10-19 (refs #2) firmware: set more effective PID coefficients.
    * (refs #2) scheme: Back R16 to 10 Ohm to make regulation easy.
    * (refs #2) tools: fix datatype conversion.
    * (refs #2) firmware: set more effective PID coefficients.
    * (refs #2) Added simple filter on speed warning.
    [g602.kicad_pcb, g602.sch]
2019-10-20 (refs #6) firmware: Stop blinking on speed error when autostop triggered.
    [Ctrl.ino]
2019-12-12 (refs #none) refactored (#10)
    * (refs #) tools: added some good buttons.
    * (refs #) tools: refactored.
    * (refs #) firmware: namespace changed.
